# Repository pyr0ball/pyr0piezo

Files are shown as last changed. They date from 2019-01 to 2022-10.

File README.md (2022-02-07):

For more extensive documentation, refer to the [Docs Site](https://docs.pyroballpcbs.com) (source included in this repository)

Presenting...

---

# The Pyr0-Piezo Z-Axis Sensor

## What is this thing?

TL;DR: It's a litte circuit that turns your actual nozzle into a z-probe.

This is a Z-Probe Sensor for 3D Printers that utilizes a piezoelectric element (commonly a 20-27mm piezo disk used in musical pickups) to detect when the nozzle of the printer touches the bed. There have been other Z-Probes in the past that do this, but this is the first to incorporate an onboard microcontroller that automatically calibrates and balances the circuit. Previous piezo Z-Probes all required manual tuning to some extent, usually with tiny hard-to-use trimpots. Due to the mechanical and electrical characteristics of this type of sensor, it has several advantages over other Z-Probes:

- There are no offsets to configure or adjust
- It can be configured to emulate either a standard endstop, or any active-high Z-Probe
- It's not dependent on a specific type of bed or hotend
- The builtin signal filtering reduces the amount of false driggers dramatically compared to other piezo sensors.
- It's FAST. Delay between the piezo being actuated and the z-trigger signal being sent to the printer's controller is ***just 26 nanoseconds***

### Is there a catch?

Well, yeah a couple. The sensor requires introducing a small amount of physical instability into the construction of the 3D printer. Something needs to move, even a small fraction of a millimeter. This can be something like the bed being pushed down slightly on it's springs, or adding a hinge and a tensioning spring to the print head. There's innumerable ways to make this work, and I've been working hard with my beta testers to find the best possible method combining as much stability as possble with the highest sensitivity. The other catch is that any oozing filament will skew the leveling results, so you have to decide to either assume there will always be ooze and use a small z-offset, or add a nozzle wipe/clean manuver to your startup gcode before bed leveling.

### How do I use it?

I designed the sensor to connect to a 3D Printer's controller like any other endstop or Z-Probe. The sensor also includes an i2c interface that will allow the 3D Printer's controller to change parameters on the fly depending on the use-case.

The piezo element is mounted somewhere on the 3D Printer in such a way that it undergoes mechanical stress when the nozzle touches the bed. So far there have been three distinct mounting schemes that appear to work well:

- On the extruder assembly
- Under the Print Bed
- In the case of CoreXY or other Gantry Kinematic systems, on either end of the gantry

#### Features:

- Self-calibrating (no more fiddling with tiny potentiometers!)
- Ultra-precise z-height measurements
- Zero offset (The nozzle itself is the sensor!)
- Compatible with ALL surface types
- No plugging in removable sensors for leveling
- Tunable over UART / I2C

#### FFC Cable Chain Extra Features:

- FFC Cable chain for a clean connection between print head and controller
- Onboard switchable DC buck converter for 12v or 5v fan operation
- LED Feedback on all PWM components
 Standalone version available for drop-in installation

Credit must be given to precisionpiezo.co.uk for getting me started on this project and giving me a place to start. I did build a version of the FFC cable chain based on their electrical designs but found the calibration of the circuit to be very fiddly, as the range of value on the potentiometers that was acceptable was very narrow.

I've since started from scratch using my own BOM and designs, while including an onboard microcontroller to handle auto-calibration. Given that every 3D printer is different, I wanted this sensor to be as easy and stable as other sensors available on the market, but with the increased performance of a piezo sensor.

Join our discord for support and to join in realtime discussion for the project:

Discord Banner 1

---

## Contribution:

Please submit all Pull Requests through the **develop** branch!

The support site for this project uses a script to automatically parse git commits for changelog data. There are three categories of commits that should show up in the case log:

- Bugfix `#bugfix`: commits related to fixing something that's broken
- Added Features `#featureadd`: Commits related to adding new functions and features
- Documentation `#docs`: Any commits that deal specifically with the [documentation site](https://docs.pyroballpcbs.com) or comments/instructions contained within the source itself but do not contribute any functional changes

Simply by adding the corresponding tag to the end of the first line of your commit message, the changelog will automatically compile these for the documentation site. Please be sure to include this in any commit messages for this project.

I would also request that commits remain small, adding each change/fix/feature to their own commits. This will help with future debugging, version tracking, and testing.

---

This is a complete redesign from the ground up, but was inspired by the sensor developed by [PrecisionPiezoUK](https://precisionpiezo.co.uk/resources-osh)

Original FFC Cable Chain designs can be found on my Thingiverse:

- [3D Printed Mount for Prusa/Anet printers](https://www.thingiverse.com/thing:2712439)
- [FFC Cable Chain + Piezo boards](https://www.thingiverse.com/thing:2618717)

 Please refer to LICENSE.md for license information

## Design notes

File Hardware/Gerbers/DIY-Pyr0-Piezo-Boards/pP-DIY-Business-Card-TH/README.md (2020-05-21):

# Pyr0-Piezo DIY BusinessCard

This variant of the Pyr0-Piezo circuit utilizes an all Through-Hole design, allowing users to easily solder in their own components.

This circuit also features a full breakout of all of the pins required to connect an external Arduino if the user doesn't want to use an integrated one.

Programming can be performed initially over the onboard ICSP header, and after a bootloader is installed, the user may reprogram the Atmega over the UART header. Alternatively, if the user owns an Arduino Uno with a DIL socket, the Atmega can be programmed using that board and transferred to this one afterward.

Pin assignments are shown on the silkscreen for each header

TODO: Add pin assignments and images

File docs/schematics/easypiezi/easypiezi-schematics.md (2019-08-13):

### EasyPiezi v1.0.0 Schematic

<object data="../Pyr0-Piezo_Standalone_1.0.0_Schematic.pdf" type="application/pdf" width="100%" height="450px">
    <embed src="../Pyr0-Piezo_Standalone_1.0.0_Schematic.pdf">
        <p>This browser does not support PDFs. Please download the PDF to view it: <a href="../Pyr0-Piezo_Standalone_1.0.0_Schematic.pdf">Download PDF</a>.</p>
    </embed>
</object>

### EasyPiezi v1.0.2 Schematic

<object data="../Pyr0-Piezo_Standalone_1.0.2_Schematic.pdf" type="application/pdf" width="100%" height="450px">
    <embed src="../Pyr0-Piezo_Standalone_1.0.2_Schematic.pdf">
        <p>This browser does not support PDFs. Please download the PDF to view it: <a href="../Pyr0-Piezo_Standalone_1.0.2_Schematic.pdf">Download PDF</a>.</p>
    </embed>
</object>

### EasyPiezi v1.1.1 Schematic

<object data="../Pyr0-Piezo_Standalone_PT100_1.1.1_Schematic.pdf" type="application/pdf" width="100%" height="450px">
    <embed src="../Pyr0-Piezo_Standalone_PT100_1.1.1_Schematic.pdf">
        <p>This browser does not support PDFs. Please download the PDF to view it: <a href="../Pyr0-Piezo_Standalone_PT100_1.1.1_Schematic.pdf">Download PDF</a>.</p>
    </embed>
</object>

### EasyPiezi v2.0.0 Schematic

<object data="../Pyr0-Piezo_Standalone_PT100_2.0.0_Schematic.pdf" type="application/pdf" width="100%" height="450px">
    <embed src="../Pyr0-Piezo_Standalone_PT100_2.0.0_Schematic.pdf">
        <p>This browser does not support PDFs. Please download the PDF to view it: <a href="../Pyr0-Piezo_Standalone_PT100_2.0.0_Schematic.pdf">Download PDF</a>.</p>
    </embed>
</object>

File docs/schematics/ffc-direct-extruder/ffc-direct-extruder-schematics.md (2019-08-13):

### FFC Direct Extruder v1.0.2 Schematic

<object data="../Pyr0-Piezo_FFC_Extruder_Board1.0.2_Schematic.pdf" type="application/pdf" width="100%" height="450px">
    <embed src="../Pyr0-Piezo_FFC_Extruder_Board1.0.2_Schematic.pdf">
        <p>This browser does not support PDFs. Please download the PDF to view it: <a href="../Pyr0-Piezo_FFC_Extruder_Board1.0.2_Schematic.pdf">Download PDF</a>.</p>
    </embed>
</object>

### FFC Direct Extruder v1.1.0 Schematic

<object data="../Pyr0-Piezo_FFC_Extruder_Board1.1.0_Schematic.pdf" type="application/pdf" width="100%" height="450px">
    <embed src="../Pyr0-Piezo_FFC_Extruder_Board1.1.0_Schematic.pdf">
        <p>This browser does not support PDFs. Please download the PDF to view it: <a href="../Pyr0-Piezo_FFC_Extruder_Board1.1.0_Schematic.pdf">Download PDF</a>.</p>
    </embed>
</object>

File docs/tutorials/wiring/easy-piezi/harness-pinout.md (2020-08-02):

# EasyPiezi Wiring Harness Pinout

## Main Connector Controller Side

The Main Connector for the EasyPiezi has 6 pins, with Pin1 marked with a small embossed arrow:

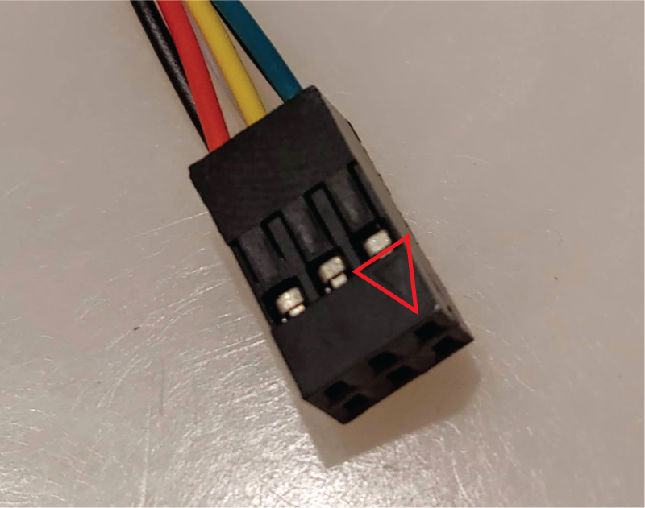
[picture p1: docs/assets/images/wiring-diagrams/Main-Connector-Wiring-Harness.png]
Main Connecctor Wiring Harness Input


Pin numbers are laid out in the following image and table:

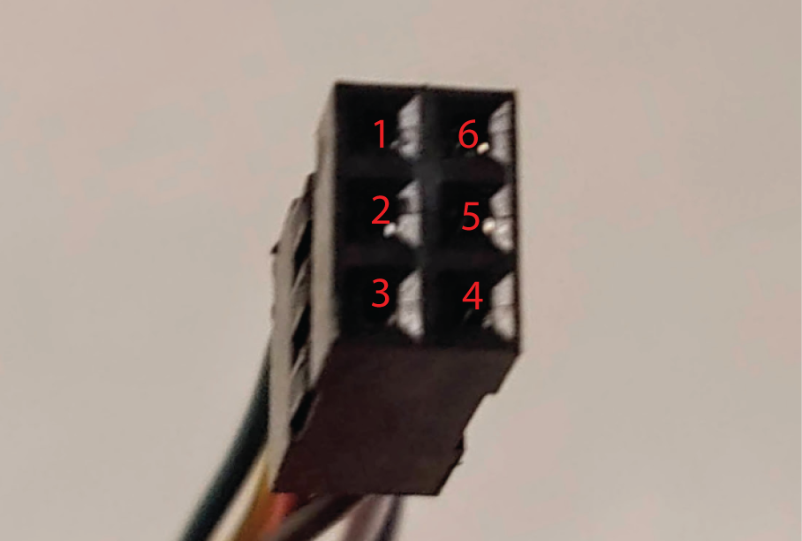
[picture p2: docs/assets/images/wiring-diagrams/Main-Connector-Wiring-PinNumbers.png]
Input Connector Pin Assignments


| Pin Number | Wire Color | Signal Name | Req/Opt |
|---|---|---|---|
| 1 | <strong><span style="color:green">Green</span></strong> | SDA (I2C) | Optional|
| 2 | <strong><span style="color:yellow; background-color:#212121; ">Yellow</span></strong> | SCL (I2C) | Optional|
| 3 | <strong><span style="color:red">Red</span></strong> | +6-12V DC | Required|
| 4 | <strong><span style="color:black; background-color:#F5F5F5;">Black</span></strong> | Ground | Required|
| 5 | <strong><span style="color:white; background-color:#212121">White</strong> | Z-Trigger | Required|
| 6 | <strong><span style="color:#08F">Blue</strong> | PT100 Anlg  | Optional|

## Main Connector Sensor Side

The EasyPiezi's Main Connector Pinout is printed on the bottom of the board:

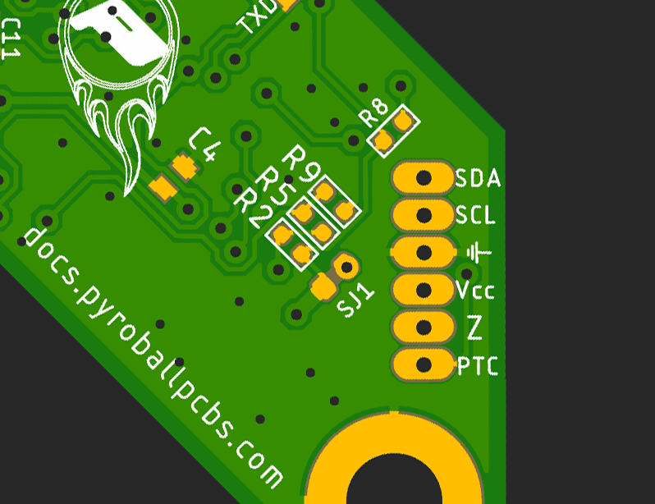
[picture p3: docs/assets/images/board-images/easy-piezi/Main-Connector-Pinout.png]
EasyPiezi Board Main Connector Pinout


They are arranged from top to bottom:

| Pin Number | Wire Color | Signal Name | Req/Opt |
|---|---|---|---|
| 1 | <strong><span style="color:green">Green</span></strong> | SDA (I2C) | Optional|
| 2 | <strong><span style="color:yellow; background-color:#212121; ">Yellow</span></strong> | SCL (I2C) | Optional|
| 3 | <strong><span style="color:black; background-color:#aaa;">Black</span></strong> | Ground | Required|
| 4 | <strong><span style="color:red">Red</span></strong> | +6-12V DC | Required|
| 5 | <strong><span style="color:white; background-color:#212121">White</strong> | Z-Trigger | Required|
| 6 | <strong><span style="color:#08F">Blue</strong> | PT100 Anlg  | Optional|

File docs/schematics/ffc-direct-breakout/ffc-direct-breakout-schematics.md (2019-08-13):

### FFC Direct Breakout v1.0.0 Schematic

<object data="../Pyr0-Piezo_FFC_Breakout_1.0.0_Schematic.pdf" type="application/pdf" width="100%" height="450px">
    <embed src="../Pyr0-Piezo_FFC_Breakout_1.0.0_Schematic.pdf">
        <p>This browser does not support PDFs. Please download the PDF to view it: <a href="../Pyr0-Piezo_FFC_Breakout_1.0.0_Schematic.pdf">Download PDF</a>.</p>
    </embed>
</object>

### FFC Direct Breakout v2.0.0 Schematic

<object data="../Pyr0-Piezo_FFC_Breakout_2.0.0_Schematic.pdf" type="application/pdf" width="100%" height="450px">
    <embed src="../Pyr0-Piezo_FFC_Breakout_2.0.0_Schematic.pdf">
        <p>This browser does not support PDFs. Please download the PDF to view it: <a href="../Pyr0-Piezo_FFC_Breakout_2.0.0_Schematic.pdf">Download PDF</a>.</p>
    </embed>
</object>

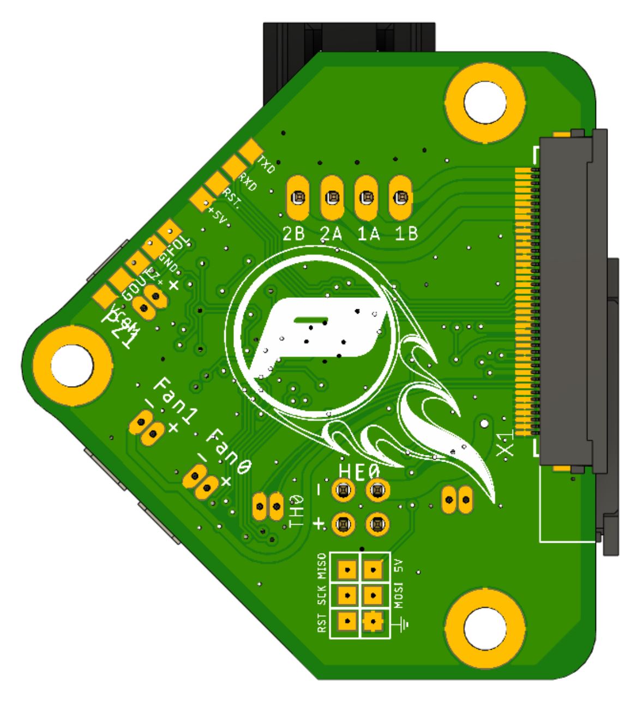
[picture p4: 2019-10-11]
docs/assets/images/board-images/pp-ffc/Pyr0-Piezo-FFC-Direct-Extruder_v2.1.2_Bot.JPG

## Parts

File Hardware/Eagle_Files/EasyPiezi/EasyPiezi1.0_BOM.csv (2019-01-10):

Qty | Value | Device | Package | Parts | Description | AVAILABILITY | DESCRIPTION | MANUFACTURER_PART_NUMBER | MF | MP | MPN | OC_FARNELL | OC_NEWARK | PACKAGE | PRICE | TP_SIGNAL_NAME | VALUE | VENDOR
4 |  | SEEED-LED_SMD-LED-CLEAR-BLUE(0603)LED_0603 | SEEED-LED_LED-0603 | ERR, PWR, TRG, Z_TRG | 304090045
3 |  | SMD-RES-0R-5%-1/16W(0402) | R0402 | R6, R8, R16 | 301010000 |  |  |  |  |  | RC0402JR-070RL |  |  |  |  |  | 0R
1 | 0.1uF | CERAMIC-1NF-50V-10%-X7R(0402)CAP_0402 | CAPC1005X50 | C3 | 302010005
1 | 100R | SMD-RES-0R-5%-1/16W(0402) | R0402 | R15 | 301010000 |  |  |  |  |  | RC0402JR-070RL |  |  |  |  |  | 0R
3 | 10K | SMD-RES-0R-5%-1/16W(0402) | R0402 | R3, R5, R10 | 301010000 |  |  |  |  |  | RC0402JR-070RL |  |  |  |  |  | 0R
2 | 1M | SMD-RES-0R-5%-1/16W(0402) | R0402 | R1, R4 | 301010000 |  |  |  |  |  | RC0402JR-070RL |  |  |  |  |  | 0R
2 | 1uF | SEEED-CAPACITOR_CERAMIC-10UF-25V-10%-X5R(0805)CAP_0603_GEN | CAPC1609X80 | C1, C2 | 302010178
2 | 220R | SMD-RES-0R-5%-1/16W(0402) | R0402 | R9, R11 | 301010000 |  |  |  |  |  | RC0402JR-070RL |  |  |  |  |  | 0R
1 | 3.3K | SMD-RES-0R-5%-1/16W(0402) | R0402 | R2 | 301010000 |  |  |  |  |  | RC0402JR-070RL |  |  |  |  |  | 0R
2 | 330R | SMD-RES-0R-5%-1/16W(0402) | R0402 | R12, R13 | 301010000 |  |  |  |  |  | RC0402JR-070RL |  |  |  |  |  | 0R
1 | 470R | SMD-RES-0R-5%-1/16W(0402) | R0402 | R14 | 301010000 |  |  |  |  |  | RC0402JR-070RL |  |  |  |  |  | 0R
1 | 680R | SMD-RES-0R-5%-1/16W(0402) | R0402 | R7 | 301010000 |  |  |  |  |  | RC0402JR-070RL |  |  |  |  |  | 0R
1 | ATMEGA48PA-MMHR28M1-L | ATMEGA48PA-MMHR28M1-L | 28M1-L | U1 |  |  |  | ATMEGA48PAMMHR |  |  |  |  |  |  |  |  |  | Atmel
1 | BAV199 | BAV199 | SOT23 | D8 | DIODE
1 | CON-MOLEX-2P-1.27MM048 | CON-MOLEX-2P-1.27MM048 | 53048-02 | PZ1 | CONNECTOR |  |  |  | MOLEX |  | 53048-0210 | 1012259 | 57H4718
1 | CON-MOLEX-3P-1.25MM048 | CON-MOLEX-3P-1.25MM048 | 53048-03 | J1 | CONNECTOR |  |  |  | WALDOM/MOLEX |  | 53048-0310 | 9732918 | 38C9908
2 | HOLES_MOUNT-PAD-ROUND2.8 | HOLES_MOUNT-PAD-ROUND2.8 | HOLES_2,8-PAD | H2, H3 | MOUNTING PAD, round
1 | L78L05ACU | L78L05ACU | SOT89 | U2 | 5V Positive voltage regulator SMD SOT89 Package | Unavailable | Voltage regulator | fixed | 5V | 0.1A | SOT89 | SMD | Package: reel, tape |  | STMicroelectronics | L78L05ACU-TR
1 | LM358PWRDFN-8 | LM358PWRDFN-8 | SON50P200X200X60-9N | U3
1 | MCP6001T-I/OTSOT-23-5_MC-L | MCP6001T-I/OTSOT-23-5_MC-L | SOT-23-5_MC-L | U4 |  |  |  | MCP6001TIOT |  |  |  |  |  |  |  |  |  | Microchip
2 | TPTP06R | TPTP06R | TP06R | INT, SS | Test pad
13 | TPTP13SQ | TPTP13SQ | TP13SQ | +5V, 5V, GND, MISO, MOSI, RST, RST., RXD, SCK, SCL, SDA, TXD, ⏚ | Test pad

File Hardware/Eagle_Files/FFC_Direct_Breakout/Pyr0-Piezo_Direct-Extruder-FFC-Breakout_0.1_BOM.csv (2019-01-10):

Qty | Value | Device | Package | Parts | Description | AVAILABILITY | DESCRIPTION | MANUFACTURER_PART_NUMBER | MF | MP | MPN | OC_FARNELL | OC_NEWARK | PACKAGE | PRICE | VALUE | VENDOR
2 |  | KK-156-2 | KK-156-2 | HE0, PWR | KK 156 HEADER |  |  |  | MOLEX |  |  | unknown | unknown
2 |  | LEDCHIP-LED0805 | CHIP-LED0805 | 5V, 12V | LED
1 |  | SEEED-SWITCH_DIP-TOGGLE-SWITCH-2CH-(2X3P-2.54)DPDT_254_6P_UPDATE | SEEED-SWITCH_SW6-2.54-9.0X3.5X3.2+2.0MM | SW1 | 311010004
1 | 100R | SMD-RES-2K-5%-1/8W(0805) | R0805 | R5 | 301010318 |  |  |  |  |  | RC0805JR-072KL |  |  |  |  | 2K
1 | 10R | SMD-RES-2K-5%-1/8W(0805) | R0805 | R7 | 301010318 |  |  |  |  |  | RC0805JR-072KL |  |  |  |  | 2K
1 | 10uF | SEEED-CAPACITOR_CERAMIC-10UF-25V-10%-X5R(0805)CAP_0805-3D | CAPC2012X130 | C5 | 302010178
1 | 1K | SEEED-RESISTOR_SMD-RES-1.5K-1%-1/10W(0603)DETAILED_MODEL | SEEED-RESISTOR_R0603 | R4 | 301010189
1 | 1R | SMD-RES-2K-5%-1/8W(0805) | R0805 | R6 | 301010318 |  |  |  |  |  | RC0805JR-072KL |  |  |  |  | 2K
1 | 2.05K | SEEED-RESISTOR_SMD-RES-1.5K-1%-1/10W(0603)DETAILED_MODEL | SEEED-RESISTOR_R0603 | R3 | 301010189
4 | 220uf | DIP-ALUMINUM-100UF-16V(D5-H7MM) | PC-D5.3MM | C1, C2, C3, C4 | 302030031 |  |  |  |  |  | KS 100uF/16V |  |  |  |  | 100uf
1 | 240R | SEEED-RESISTOR_SMD-RES-1.5K-1%-1/10W(0603)DETAILED_MODEL | SEEED-RESISTOR_R0603 | R1 | 301010189
1 | 2N2222TO92 | 2N2222TO92 | TO92 | Q1 | NPN TRANSISTOR
1 | 2N2907 | 2N2907 | TO92 | Q2 | NPN TRANSISTOR
1 | 715R | SEEED-RESISTOR_SMD-RES-1.5K-1%-1/10W(0603)DETAILED_MODEL | SEEED-RESISTOR_R0603 | R2 | 301010189
4 | C-GRID-02-70553 | C-GRID-02-70553 | 70553-02 | FAN0, FAN1, TH0, Z_MIN | CONNECTOR |  |  |  | MOLEX |  |  | unknown | unknown
1 | C-GRID-04-70553 | C-GRID-04-70553 | 70553-04 | E0 | CONNECTOR |  |  |  | MOLEX |  |  | unknown | unknown
4 | HOLES_MOUNT-PAD-ROUND3.2 | HOLES_MOUNT-PAD-ROUND3.2 | HOLES_3,2-PAD | H1, H2, H3, H4 | MOUNTING PAD, round
1 | L78L05ACU | L78L05ACU | SOT89 | U2 | 5V Positive voltage regulator SMD SOT89 Package | Unavailable | Voltage regulator | fixed | 5V | 0.1A | SOT89 | SMD | Package: reel, tape |  | STMicroelectronics | L78L05ACU-TR
1 | LM317DCY | LM317DCY | SOT230P700X180-4N | U1 | IC ADJ LINEAR REG 1.25V TO 37V | Unavailable | IC Regulator LM317/SOT223/LM317DCY TEXAS INSTRUMENT RoHS Ampere=1.5 SOT223 |  | Texas Instruments | LM317DCY |  |  |  | SOT-223-4 Texas Instruments | None
1 | SFW24R-1STE1LF | SFW24R-1STE1LF | CON24_1X24_DRB_SFW | J1 |  |  |  | SFW24R1STE1LF |  |  |  |  |  |  |  |  | FCI

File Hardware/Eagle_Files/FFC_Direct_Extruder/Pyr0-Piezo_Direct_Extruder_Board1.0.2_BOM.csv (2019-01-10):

Qty | Value | Device | Package | Parts | Description | MANUFACTURER_PART_NUMBER | MF | MPN | OC_FARNELL | OC_NEWARK | TP_SIGNAL_NAME | VALUE | VENDOR
7 |  | SEEED-LED_SMD-LED-CLEAR-BLUE(0603)LED_0603 | SEEED-LED_LED-0603 | D2, D3, D4, D5, ERR, PWR, TRG | 304090045
1 |  | SMD-RES-0R-5%-1/16W(0402) | R0402 | R6 | 301010000 |  |  | RC0402JR-070RL |  |  |  | 0R
2 | 0.1uF | CERAMIC-1NF-50V-10%-X7R(0402)CAP_0402 | CAPC1005X50 | C1, C2 | 302010005
1 | 0R | SEEED-RESISTOR_SMD-RES-1.5K-1%-1/10W(0603)DETAILED_MODEL | SEEED-RESISTOR_R0603 | R14 | 301010189
1 | 100R | SMD-RES-0R-5%-1/16W(0402) | R0402 | R13 | 301010000 |  |  | RC0402JR-070RL |  |  |  | 0R
3 | 10K | SMD-RES-0R-5%-1/16W(0402) | R0402 | R2, R4, R10 | 301010000 |  |  | RC0402JR-070RL |  |  |  | 0R
2 | 1K | SMD-RES-0R-5%-1/16W(0402) | R0402 | R3, R8 | 301010000 |  |  | RC0402JR-070RL |  |  |  | 0R
2 | 1M | SMD-RES-0R-5%-1/16W(0402) | R0402 | R1, R19 | 301010000 |  |  | RC0402JR-070RL |  |  |  | 0R
1 | 1N4148DFN-1006-2 | 1N4148DFN-1006-2 | DIOC1006X70 | D1 | DIODE
1 | 1uF | SEEED-CAPACITOR_CERAMIC-10UF-25V-10%-X5R(0805)CAP_0603_GEN | CAPC1609X80 | C3 | 302010178
2 | 220R | SMD-RES-0R-5%-1/16W(0402) | R0402 | R7, R11 | 301010000 |  |  | RC0402JR-070RL |  |  |  | 0R
1 | 3.3K | SMD-RES-0R-5%-1/16W(0402) | R0402 | R17 | 301010000 |  |  | RC0402JR-070RL |  |  |  | 0R
2 | 330R | SMD-RES-0R-5%-1/16W(0402) | R0402 | R5, R12 | 301010000 |  |  | RC0402JR-070RL |  |  |  | 0R
1 | 470R | SMD-RES-0R-5%-1/16W(0402) | R0402 | R9 | 301010000 |  |  | RC0402JR-070RL |  |  |  | 0R
1 | 680R | SMD-RES-0R-5%-1/16W(0402) | R0402 | R15 | 301010000 |  |  | RC0402JR-070RL |  |  |  | 0R
1 | ATMEGA48PA-MMHR28M1-L | ATMEGA48PA-MMHR28M1-L | 28M1-L | U1 |  | ATMEGA48PAMMHR |  |  |  |  |  |  | Atmel
1 | BAV199 | BAV199 | SOT23 | D8 | DIODE
1 | C-GRID-04-70553 | C-GRID-04-70553 | 70553-04 | E0 | CONNECTOR |  | MOLEX |  | unknown | unknown
4 | CON-MOLEX-2P-1.27MM048 | CON-MOLEX-2P-1.27MM048 | 53048-02 | FAN0, FAN1, PZ1, TH0 | CONNECTOR |  | MOLEX | 53048-0210 | 1012259 | 57H4718
3 | HOLES_MOUNT-PAD-ROUND2.8 | HOLES_MOUNT-PAD-ROUND2.8 | HOLES_2,8-PAD | H1, H2, H3 | MOUNTING PAD, round
1 | JST-2.54-2X2JST-DUPONT-2.54-2X2 | JST-2.54-2X2JST-DUPONT-2.54-2X2 | HDRRAR4W64P254_2X2_556X736X556B | HE0
1 | LM358PWRDFN-8 | LM358PWRDFN-8 | SON50P200X200X60-9N | U3
1 | MCP6001T-I/OTSOT-23-5_MC-L | MCP6001T-I/OTSOT-23-5_MC-L | SOT-23-5_MC-L | U2 |  | MCP6001TIOT |  |  |  |  |  |  | Microchip
1 | SFW24R-1STE1LF | SFW24R-1STE1LF | CON24_1X24_DRB_SFW | J1 |  | SFW24R1STE1LF |  |  |  |  |  |  | FCI
2 | TPTP06R | TPTP06R | TP06R | INT, SS | Test pad
3 | TPTP10R | TPTP10R | TP10R | ADJ+, ADJ-, A_OUT | Test pad
13 | TPTP13SQ | TPTP13SQ | TP13SQ | +5V, 5V, GND, MISO, MOSI, RST, RST., RXD, SCK, SCL, SDA, TXD, ⏚ | Test pad

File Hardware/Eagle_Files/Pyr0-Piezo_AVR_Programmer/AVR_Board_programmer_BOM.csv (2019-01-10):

Qty | Value | Device | Package | Parts | Description | DESCRIPTION | DIGI-KEY_PART_NUMBER | DIGI-KEY_PURCHASE_URL | MF | MP | MPN | PACKAGE | VALUE
3 |  | SEEED-LED_SMD-LED-CLEAR-BLUE(0603)LED_0603 | SEEED-LED_LED-0603 | PWR, RX, TX | 304090045
1 |  | SEEED-SWITCH_SMD-BUTTON(2P-3.0X2.5X1.2+0.4MM)SW2-2.6-3X2.5X1.2 | SEEED-SWITCH_SW2-2.6-3.0X2.5X1.2+0.4MM | RESET | 311020047
2 |  | SMD-RES-0R-5%-1/16W(0402) | R0402 | R3, R8 | 301010000 |  |  |  |  |  | RC0402JR-070RL |  | 0R
1 | 10118192-0001LF | 10118192-0001LF | AMPHENOL_10118192-0001LF | J1 | Single Port 5 Contact Horizontal Right Angle Shielded Micro B USB 2.0 Connector | Conn Micro USB Type B RCP 5 POS 0.65mm Solder RA SMD 5 Terminal 1 Port T/R | 609-4613-1-ND | https://www.digikey.com/product-detail/en/amphenol-fci/10118192-0001LF/609-4613-1-ND/2785378 | Amphenol FCI | 10118192-0001LF |  | None
1 | 22K | SMD-RES-0R-5%-1/16W(0402) | R0402 | R1 | 301010000 |  |  |  |  |  | RC0402JR-070RL |  | 0R
1 | 47K | SMD-RES-0R-5%-1/16W(0402) | R0402 | R2 | 301010000 |  |  |  |  |  | RC0402JR-070RL |  | 0R
1 | CP2102N-A01-GQFN20 | CP2102N-A01-GQFN20 | SILABS_QFN20 | U1 | Ic Bridge Usb To Uart 20qfn | Usb-Uart Interface Bridge, Qfn-20 | 336-3692-ND | https://www.digikey.com/product-detail/en/silicon-labs/CP2102N-A01-GQFN20/336-3692-ND/6012517 | Silicon Labs | CP2102N-A01-GQFN20 |  | QFN-20 Silicon Labs
3 | HOLES_MOUNT-PAD-ROUND2.8 | HOLES_MOUNT-PAD-ROUND2.8 | HOLES_2,8-PAD | H1, H2, H3 | MOUNTING PAD, round
1 | JST-2.54MM_5P-2.54JST_2.54MM_5P_F | JST-2.54MM_5P-2.54JST_2.54MM_5P_F | HDRVR5W64P254_1X5_1270X254X575B | TTL
1 | SP0503BAHTG | SP0503BAHTG | SOT143 | D1 | TVS DIODE 5.5VWM 8.5VC SOT143 | SP050xBA Series 8 V 30 pF Uni-Directional SMT TVS Avalanche Diode Array SOT-143 | F2715CT-ND | https://www.digikey.com/product-detail/en/littelfuse-inc/SP0503BAHTG/F2715CT-ND/1154322 | Littelfuse Inc. | SP0503BAHTG |  | SOT-143 Littelfuse
5 | TP | TP | TP13SQ-HOLE | +5V, GND, RST., RXD, TXD | Test pad

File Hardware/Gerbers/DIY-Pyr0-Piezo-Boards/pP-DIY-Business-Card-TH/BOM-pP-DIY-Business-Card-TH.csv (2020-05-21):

Qty | Value | Package | References | Description | MF | MPN | OC_DIGIKEY | OC_FARNELL | OC_NEWARK | SPICEPREFIX
7 | 0.1uF | TH | C1, C2, C3, C4, C17, C18, C19 | CAPACITOR, European symbol |  |  | 2368-CML104M50-ND |  |  | C
3 | 100R | TH | R10, R12, R17 | RESISTOR, European symbol |  |  | RMCF0805JT100RCT-ND |  |  | R
6 | 10K | TH | R5, R6, R9, R15, R16, R18 | RESISTOR, European symbol |  |  | CR0805-JW-103ELFCT-ND |  |  | R
1 | 10nF | TH | C20 | CAPACITOR, European symbol |  |  | 2368-CML103M50-ND |  |  | C
2 | 10uF | TH | C21, C23 | CAPACITOR, European symbol |  |  | 478-7366-1-ND |  |  | C
5 | 1K | TH | R1, R3, R4, R7, R11 | RESISTOR, European symbol |  |  | RMCF0805JT1K00CT-ND |  |  | R
2 | 1M | TH | R2, R8 | RESISTOR, European symbol |  |  | CR0805-JW-105ELFCT-ND |  |  | R
2 | 1N4004 | TH | D1, D2 | DIODE |  |  |  |  |  | D
3 | 1uF | TH | C16, C22, C24 | CAPACITOR, European symbol |  |  | 2368-CML105M50-ND |  |  | C
2 | 2K2 | TH | R13, R14 | RESISTOR, European symbol |  |  | RMCF0805JT2K20CT-ND |  |  | R
1 | 3K3 | TH | R20 | RESISTOR, European symbol |  |  | RMCF0805JT3K30CT-ND |  |  | R
1 | 4K7 | TH | R19 | RESISTOR, European symbol |  |  | RMCF0805JT4K70CT-ND |  |  | R
1 | ATMEGA328P | DIP28 | U2 |  |  |  | ATMEGA328-PU-ND |  |  | U
2 | C-GRID-02-70553 | 70553-02 | PT100, PZ-IN | CONNECTOR | MOLEX |  |  | unknown | unknown
1 | JST-2.54MM_3PX2JST-2.54MM_3PX2 | Dupont_2x3_STR | ICSP | 2.54mm Dupont Female header 3x2p 6-positions
1 | JST-2.54MM_5P-2.54JST_2.54MM_5P_F | Dupont_1x5_RA | UART | 2.54mm Dupont Female Header 1x5p 5-positions
1 | LM2902N | DIL14 | U1 | Low power quad operational amplifier
1 | PP-STANDALONE-HEADER | Dupont_2x6_RA | J1 | 2.54mm Dupont Male Header Right 2x6 12-positions
1 | LED-3mm Green | SFH482 | PWR | 3mm LED
1 | LED-3mm Blue | SFH482 | TRIG | 3mm LED

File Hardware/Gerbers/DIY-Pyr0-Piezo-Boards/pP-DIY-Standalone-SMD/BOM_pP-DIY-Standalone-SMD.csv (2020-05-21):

Qty | References | Value | Package | Description | MF | MPN | OC_FARNELL | OC_NEWARK
1 | PWR | GREEN | LED0805 | LED SMD 0805
1 | TRIG | BLUE | LED0805 | LED SMD 0805
6 | C1, C2, C4, C17, C18, C19 | 0.1uF | C0805
3 | R10, R12, R17 | 100R | R0805
5 | R5, R6, R9, R15, R16 | 10K | R0805
1 | C20 | 10nF | C0805
2 | C21, C23 | 10uF | C0805
5 | R1, R3, R4, R7, R11 | 1K | R0805
2 | R2, R8 | 1M | R0805
1 | C16 | 1uF | C0805
2 | R13, R14 | 2K2 | R0805
2 | C22, C24 | 3.3uF | C0805
1 | R19 | 4K7 | R0805
1 | D1 | BAV99 | SOT23 | DIODE
2 | PT1, PZ | C-GRID-02-70553 | 70553-02 | CONNECTOR | MOLEX
1 | U1 | LM2902D | SO14 | Low power quad operational amplifier
1 | J1 | PP-STANDALONE-HEADER | Dupont 2.54mm 2x6 RA

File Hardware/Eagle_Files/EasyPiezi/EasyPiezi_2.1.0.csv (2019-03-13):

Part | Value | Device | Package | Description | AVAILABILITY | DESCRIPTION | MF | MP | MPN | OC_FARNELL | OC_NEWARK | PACKAGE | PRICE | PROD_ID | TP_SIGNAL_NAME | VALUE
+5V | TPTP13SQ | TPTP13SQ | TP13SQ | Test pad
5V | TPTP13SQ | TPTP13SQ | TP13SQ | Test pad
ADJ+ | TPTP13SQ | TPTP13SQ | TP13SQ | Test pad
ADJ- | TPTP13SQ | TPTP13SQ | TP13SQ | Test pad
C1 | 1uF | SEEED-CAPACITOR_CERAMIC-10UF-25V-10%-X5R(0805)CAP_0603_GEN | CAPC1609X80 | 302010178
C2 | 1uF | SEEED-CAPACITOR_CERAMIC-10UF-25V-10%-X5R(0805)CAP_0603_GEN | CAPC1609X80 | 302010178
C3 | 0.1uF | CERAMIC-1NF-50V-10%-X7R(0402)CAP_0402 | CAPC1005X50 | 302010005
C4 | 0.1uF | CERAMIC-1NF-50V-10%-X7R(0402)CAP_0402 | CAPC1005X50 | 302010005
C5 | 0.1uF | CERAMIC-1NF-50V-10%-X7R(0402)CAP_0402 | CAPC1005X50 | 302010005
C6 | 0.1uF | CERAMIC-1NF-50V-10%-X7R(0402)CAP_0402 | CAPC1005X50 | 302010005
C7 | 1uF | CERAMIC-1NF-50V-10%-X7R(0402)CAP_0402 | CAPC1005X50 | 302010005
C8 | 0.1uF | CERAMIC-1NF-50V-10%-X7R(0402)CAP_0402 | CAPC1005X50 | 302010005
C9 | 0.1uF | CERAMIC-1NF-50V-10%-X7R(0402)CAP_0402 | CAPC1005X50 | 302010005
C10 | 0.1uF | CERAMIC-1NF-50V-10%-X7R(0402)CAP_0402 | CAPC1005X50 | 302010005
C11 | 10nF | CERAMIC-1NF-50V-10%-X7R(0402)CAP_0402 | CAPC1005X50 | 302010005
C12 | 10uF | CERAMIC-1NF-50V-10%-X7R(0402)CAP_0402 | CAPC1005X50 | 302010005
C13 | 3.3uF | CERAMIC-1NF-50V-10%-X7R(0402)CAP_0402 | CAPC1005X50 | 302010005
C14 | 10uF | CERAMIC-1NF-50V-10%-X7R(0402)CAP_0402 | CAPC1005X50 | 302010005
C15 | 3.3uF | CERAMIC-1NF-50V-10%-X7R(0402)CAP_0402 | CAPC1005X50 | 302010005
D1 | ZENER_DIODE_PLZ5V1C | ZENER_DIODE_PLZ5V1C | DO-219AC
D8 | BAV199 | BAV199 | SOT23 | DIODE
F1 | 500mA | SMD-RES-0R-5%-1/16W(0402) | R0402 | 301010000 |  |  |  |  | RC0402JR-070RL |  |  |  |  |  |  | 0R
GND | TPTP13SQ | TPTP13SQ | TP13SQ | Test pad
H2 | HOLES_MOUNT-PAD-ROUND2.8 | HOLES_MOUNT-PAD-ROUND2.8 | HOLES_2,8-PAD | MOUNTING PAD, round
H3 | HOLES_MOUNT-PAD-ROUND2.8 | HOLES_MOUNT-PAD-ROUND2.8 | HOLES_2,8-PAD | MOUNTING PAD, round
INT | TPTP06R | TPTP06R | TP06R | Test pad
J1 | CON-MOLEX-6P-1.25MM048 | CON-MOLEX-6P-1.25MM048 | 53048-06 | CONNECTOR |  |  | WALDOM/MOLEX |  | 53048-0610 | 1012260 | 38C9911
J2 |  | SEEED-RESISTOR_SMD-RES-1.5K-1%-1/10W(0603)DETAILED_MODEL | SEEED-RESISTOR_R0603 | 301010189
LED | LED-RGB-COM_ANO0606 | LED-RGB-COM_ANO0606 | 0606_LED | Everlight Electronics Co Ltd EAST1616RGBB4 0606 RGB LED |  |  |  |  |  |  |  |  |  | DIO-12140
MISO | TPTP13SQ | TPTP13SQ | TP13SQ | Test pad
MOSI | TPTP13SQ | TPTP13SQ | TP13SQ | Test pad
PT100 | CON-MOLEX-2P-1.27MM048 | CON-MOLEX-2P-1.27MM048 | 53048-02 | CONNECTOR |  |  | MOLEX |  | 53048-0210 | 1012259 | 57H4718
PZ+ | TPTP13SQ | TPTP13SQ | TP13SQ | Test pad
PZ1 | CON-MOLEX-2P-1.27MM048 | CON-MOLEX-2P-1.27MM048 | 53048-02 | CONNECTOR |  |  | MOLEX |  | 53048-0210 | 1012259 | 57H4718
R1 | 1M | SMD-RES-0R-5%-1/16W(0402) | R0402 | 301010000 |  |  |  |  | RC0402JR-070RL |  |  |  |  |  |  | 0R
R3 | 10K | SMD-RES-0R-5%-1/16W(0402) | R0402 | 301010000 |  |  |  |  | RC0402JR-070RL |  |  |  |  |  |  | 0R
R4 | 1M | SMD-RES-0R-5%-1/16W(0402) | R0402 | 301010000 |  |  |  |  | RC0402JR-070RL |  |  |  |  |  |  | 0R
R6 |  | SMD-RES-0R-5%-1/16W(0402) | R0402 | 301010000 |  |  |  |  | RC0402JR-070RL |  |  |  |  |  |  | 0R
R7 | 10K | SMD-RES-0R-5%-1/16W(0402) | R0402 | 301010000 |  |  |  |  | RC0402JR-070RL |  |  |  |  |  |  | 0R
R8 |  | SMD-RES-0R-5%-1/16W(0402) | R0402 | 301010000 |  |  |  |  | RC0402JR-070RL |  |  |  |  |  |  | 0R
R10 | 10K | SMD-RES-0R-5%-1/16W(0402) | R0402 | 301010000 |  |  |  |  | RC0402JR-070RL |  |  |  |  |  |  | 0R
R14 | 1K | SMD-RES-0R-5%-1/16W(0402) | R0402 | 301010000 |  |  |  |  | RC0402JR-070RL |  |  |  |  |  |  | 0R
R15 | 100R | SMD-RES-0R-5%-1/16W(0402) | R0402 | 301010000 |  |  |  |  | RC0402JR-070RL |  |  |  |  |  |  | 0R
R17 | 10K | SMD-RES-0R-5%-1/16W(0402) | R0402 | 301010000 |  |  |  |  | RC0402JR-070RL |  |  |  |  |  |  | 0R
R18 | 10K | SMD-RES-0R-5%-1/16W(0402) | R0402 | 301010000 |  |  |  |  | RC0402JR-070RL |  |  |  |  |  |  | 0R
R19 | 2K2 | SMD-RES-0R-5%-1/16W(0402) | R0402 | 301010000 |  |  |  |  | RC0402JR-070RL |  |  |  |  |  |  | 0R
R20 | 2K2 | SMD-RES-0R-5%-1/16W(0402) | R0402 | 301010000 |  |  |  |  | RC0402JR-070RL |  |  |  |  |  |  | 0R
R21 | 100R | SMD-RES-0R-5%-1/16W(0402) | R0402 | 301010000 |  |  |  |  | RC0402JR-070RL |  |  |  |  |  |  | 0R
R22 | 100R | SMD-RES-0R-5%-1/16W(0402) | R0402 | 301010000 |  |  |  |  | RC0402JR-070RL |  |  |  |  |  |  | 0R
RDY |  | SEEED-LED_SMD-LED-CLEAR-BLUE(0603)LED_0603 | SEEED-LED_LED-0603 | 304090045
RP1 | 1K | RESISTOR_NETWORK_X40804_L | EXBN8V-L
RST | TPTP13SQ | TPTP13SQ | TP13SQ | Test pad
RST. | TPTP13SQ | TPTP13SQ | TP13SQ | Test pad
RXD | TPTP13SQ | TPTP13SQ | TP13SQ | Test pad
SCK | TPTP13SQ | TPTP13SQ | TP13SQ | Test pad
SJ1 |  | SJM | SJM | SMD solder JUMPER
SS | TPTP06R | TPTP06R | TP06R | Test pad
TP1 | TPTP09R | TPTP09R | TP09R | Test pad
TP2 | TPTP09R | TPTP09R | TP09R | Test pad
TXD | TPTP13SQ | TPTP13SQ | TP13SQ | Test pad
U2 | L78L05ACU | L78L05ACU | SOT89 | 5V Positive voltage regulator SMD SOT89 Package | Unavailable | Voltage regulator | fixed | 5V | 0.1A | SOT89 | SMD | Package: reel, tape | STMicroelectronics | L78L05ACU-TR
U3 | LM2902QT | LM2902QT | QFN16 | Low power quad operational amplifier
U4 | ATMEGA48/88/168/328PB | ATMEGA48/88/168/328PB | QFN50P500X500X90-33N | AVR 32KBytes Flash, 1KBytes EEPROM, 2KBytes RAM, w - 20MHZ, QFN/MFL, IND TEMP, GREEN 5 V/ DFN/QFN (M) | Unavailable | AVR 32KBytes Flash, 1KBytes EEPROM, 2KBytes RAM, w - 20MHZ, QFN/MFL, IND TEMP, GREEN 5 V/ DFN/QFN _M_ | Microchip | ATMEGA328PB-MU |  |  |  | VFQFN-32 Microchip | None
⏚ | TPTP13SQ | TPTP13SQ | TP13SQ | Test pad

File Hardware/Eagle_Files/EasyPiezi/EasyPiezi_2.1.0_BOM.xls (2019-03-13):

Designator | MPN | QTY | Link
C1,C2,C7 | CL10A105KO8NNNC | 30 | https://www.digikey.com/product-detail/en/samsung-electro-mechanics/CL10A105KO8NNNC/1276-1034-2-ND/3886692
C3,C4,C5,C6,C8,C9,C10 | CL05F104ZO5NNNC | 70 | https://www.digikey.com/product-detail/en/samsung-electro-mechanics/CL05F104ZO5NNNC/1276-1004-2-ND/3886662
C11 | CL05B103KB5NFNC | 10 | https://www.digikey.com/product-detail/en/samsung-electro-mechanics/CL05B103KB5NFNC/1276-1499-2-ND/3887157
C12,C14 | GRM155C80J106ME11J | 20 | https://www.digikey.com/product-detail/en/murata-electronics-north-america/GRM155C80J106ME11J/490-18210-2-ND/9867918
C13,C15 | GRM155R60J475ME47D | 20 | https://www.digikey.com/product-detail/en/murata-electronics-north-america/GRM155R60J475ME47D/490-5915-2-ND/3694656
D1 | PLZ5V1C | 10 | https://www.digikey.com/product-detail/en/vishay-semiconductor-diodes-division/PLZ5V1C-G3-H/PLZ5V1C-G3-HGITR-ND/7594405
D8 | BAV199-7-F | 10 | https://www.digikey.com/product-detail/en/diodes-incorporated/BAV199-7-F/BAV199-FDITR-ND/1033645
F1 | ERB-RD0R50X | 10 | https://www.digikey.com/product-detail/en/panasonic-electronic-components/ERB-RD0R50X/P15122TR-ND/2796780
LED | IN-S66TATRGB | 10 | https://www.digikey.com/product-detail/en/inolux/IN-S66TATRGB/1830-1077-2-ND/7604943
R1,R4 | RMCF0402JT1M00 | 20 | https://www.digikey.com/product-detail/en/stackpole-electronics-inc/RMCF0402JT1M00/RMCF0402JT1M00TR-ND/1758203
R3,R7,R10,R17,R18 | RMCF0402JT10K0 | 50 | https://www.digikey.com/product-detail/en/stackpole-electronics-inc/RMCF0402JT10K0/RMCF0402JT10K0TR-ND/1758206
R6,R14 | CRG0402J1K0 | 20 | https://www.digikey.com/product-detail/en/te-connectivity-passive-product/CRG0402J1K0/A106129TR-ND/2389662
R8 | RC1005J332CS | 10 | https://www.digikey.com/product-detail/en/samsung-electro-mechanics/RC1005J332CS/1276-4388-2-ND/3964695
R15,R21,R22 | RMCF0402JT100R | 30 | https://www.digikey.com/product-detail/en/stackpole-electronics-inc/RMCF0402JT100R/RMCF0402JT100RTR-ND/1758155
R19,R20 | RMCF0402JT2K20 | 20 | https://www.digikey.com/product-detail/en/stackpole-electronics-inc/RMCF0402JT2K20/RMCF0402JT2K20TR-ND/1712400
RDY | LNJ812K8SRA | 10 | https://www.digikey.com/product-detail/en/panasonic-electronic-components/LNJ812K8SRA/P11472CT-ND/440504
RP1 | EXB-N8V102JX | 10 | https://www.digikey.com/product-detail/en/panasonic-electronic-components/EXB-N8V102JX/Y10102TR-ND/671522
U2 | L78L05A | 10 | https://www.digikey.com/product-detail/en/stmicroelectronics/L78L05ACUTR/497-1183-2-ND/585707
U3 | LM2902Q4T | 10 | https://www.digikey.com/product-detail/en/stmicroelectronics/LM2902Q4T/497-12417-2-ND/2832879
U4 | ATMEGA328PB-MU | 10 | https://www.digikey.com/product-detail/en/microchip-technology/ATMEGA328PB-MU/ATMEGA328PB-MU-ND/5638814

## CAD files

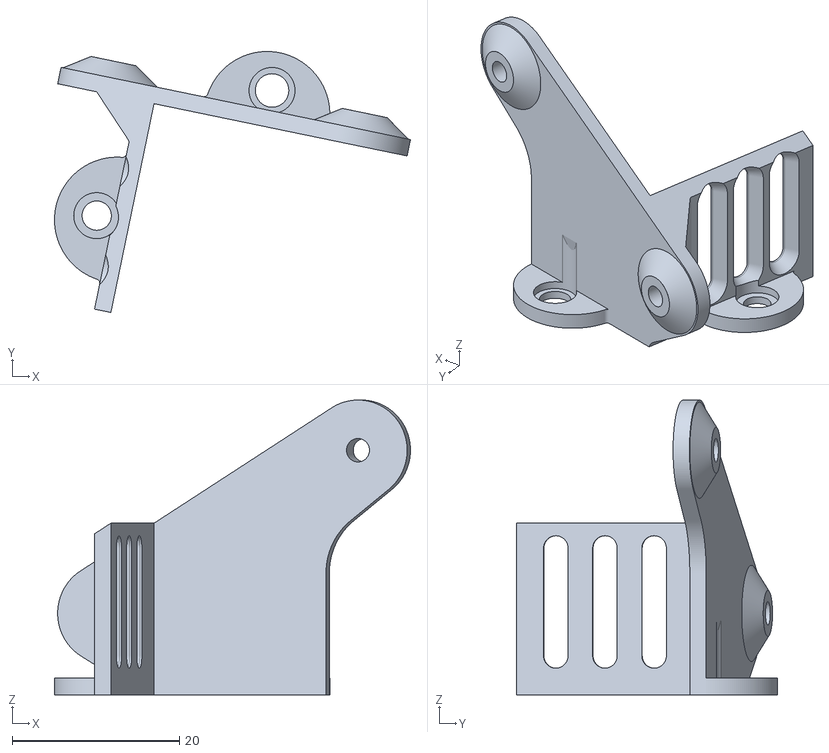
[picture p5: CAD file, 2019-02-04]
3D_Models/3D_Printed_Parts/Printer_Mounts/Creality_Series/Creality-Standalone-Board Mount.stl
42.6 x 31.2 x 35.3

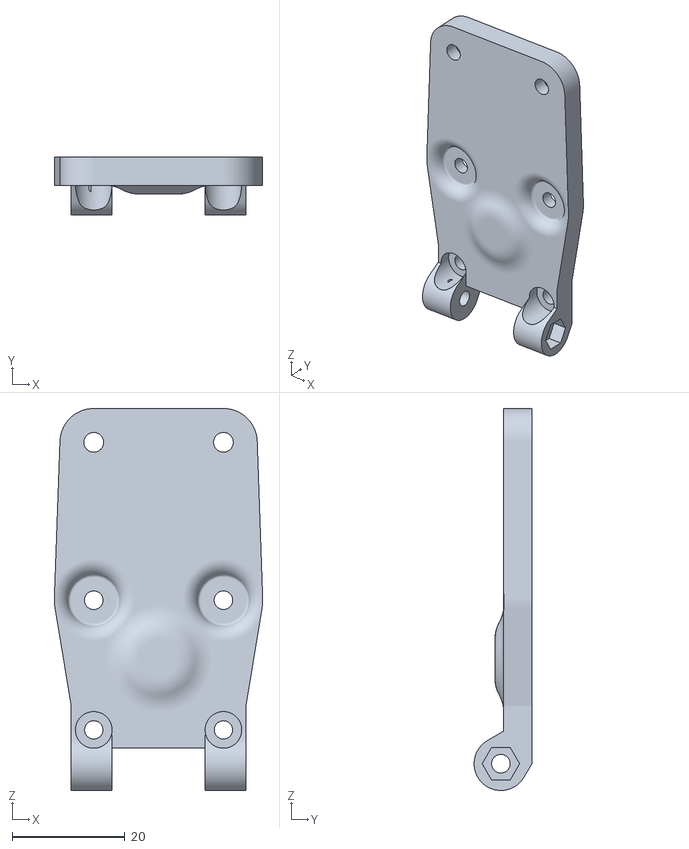
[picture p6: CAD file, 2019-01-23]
3D_Models/3D_Printed_Parts/Printer_Mounts/Prusa_i3_and_Clones/Fulcrum_20mm.stl
37.0 x 10.2 x 67.7

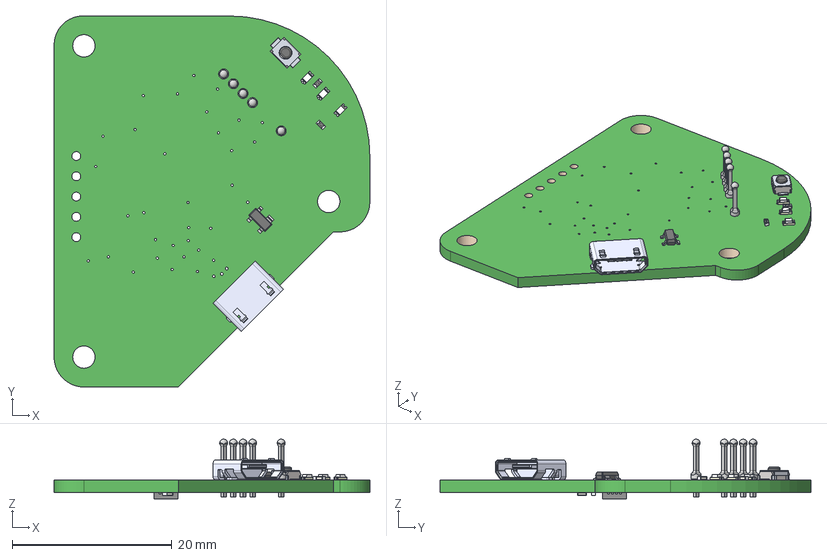
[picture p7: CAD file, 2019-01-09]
3D_Models/Board_Reference_Models/Extruder_Board_programmer.step
39.6 x 46.5 x 7.49 mm
Board
SEEED-LED_LED-0603 x 3
47K x 4
QFN-16 (3x3) Part1
QFN-16 (3x3) Part2 x 16
SP0503BAHTG
10118192-0001LF
SEEED-SWITCH_SW2-2.6-3.0X2.5X1.2+0.4MM
TP x 5

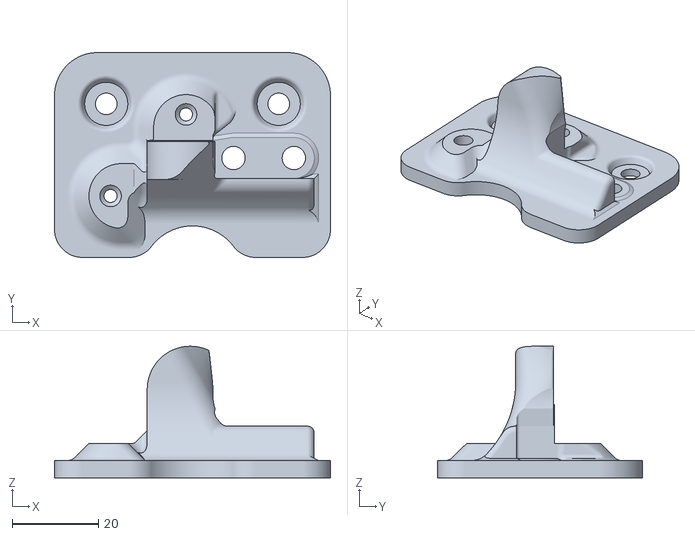
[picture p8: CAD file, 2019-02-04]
3D_Models/3D_Printed_Parts/Printer_Mounts/Creality_Series/Creality-Piezo-Plate-Mount.stl
64.0 x 47.5 x 30.5

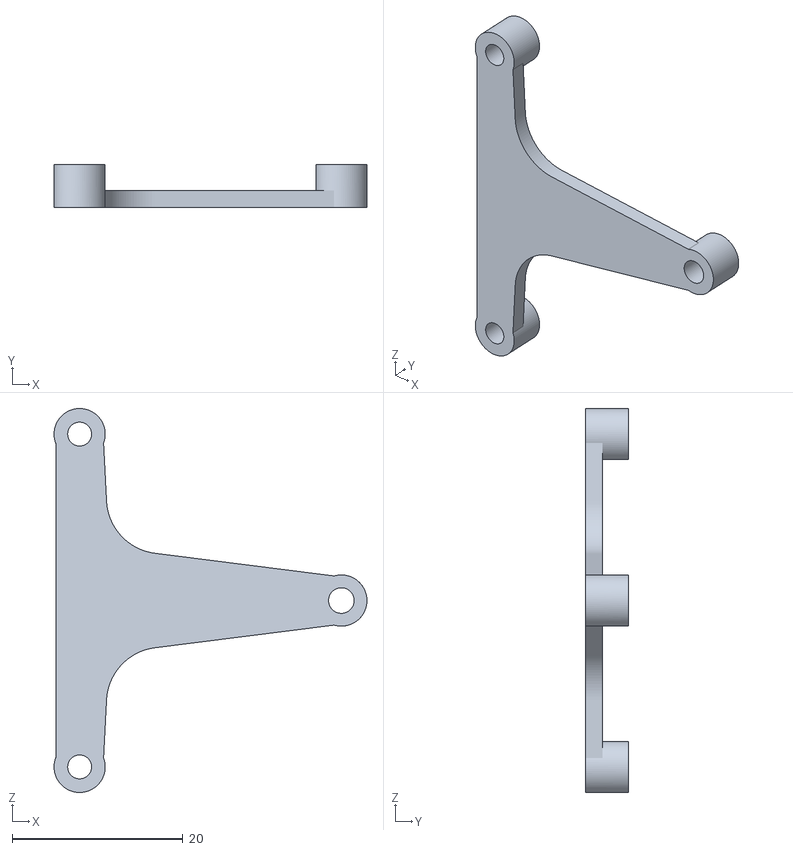
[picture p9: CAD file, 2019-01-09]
3D_Models/3D_Printed_Parts/Printer_Mounts/Prusa_i3_and_Clones/FFC_Board_Mount.stl
36.7 x 5.00 x 45.0

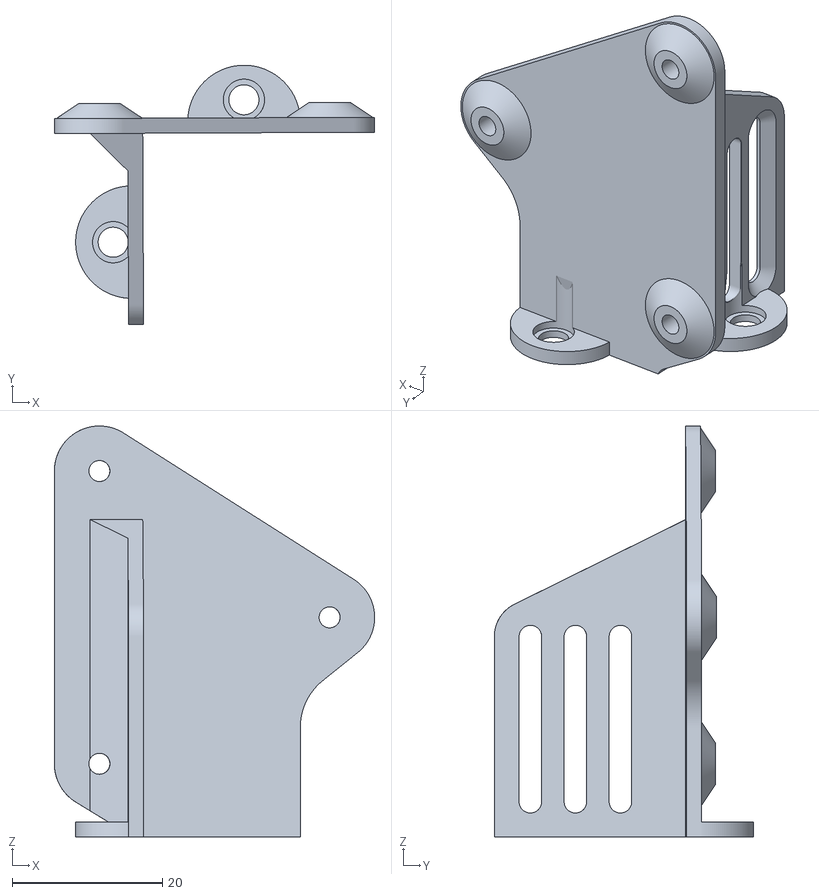
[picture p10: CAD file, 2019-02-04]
3D_Models/3D_Printed_Parts/Printer_Mounts/Creality_Series/Creality-FFC-Board Mount.stl
42.7 x 34.6 x 54.8

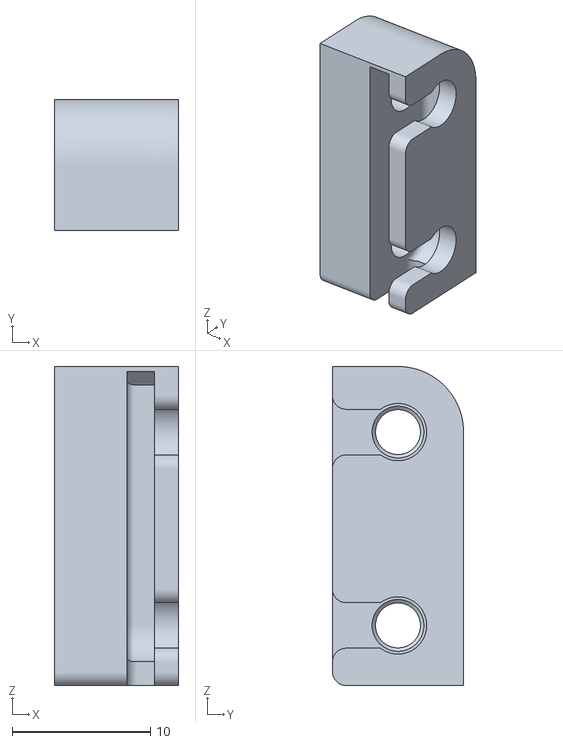
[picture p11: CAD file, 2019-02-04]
3D_Models/3D_Printed_Parts/Printer_Mounts/Creality_Series/Creality-Piezo-Nozzle-Mount.stl
9.00 x 9.50 x 23.1

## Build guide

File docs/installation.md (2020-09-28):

# Pyr0-Piezo Installation Instructions

***Important***: Every printer is different, and this sensor can be adapted to any of them, however we may not currently have a mount designed for your needs. If that's the case, please [open an issue on the github](https://github.com/pyr0ball/pyr0piezo/issues/new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) and/or send us a ping on the discord server.

## Fully Supported Printers

- [Monoprice Delta Mini](tutorials/wiring/easy-piezi/monoprice-delta-mini.md)
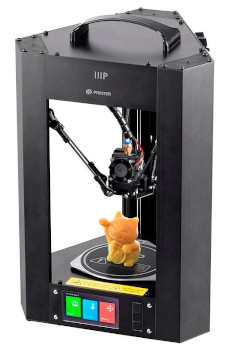
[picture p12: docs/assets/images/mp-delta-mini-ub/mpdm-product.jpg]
  - 

- [Creality Ender 3/5/Pro | CR-10](mounts/creality/creality-original-head.md)
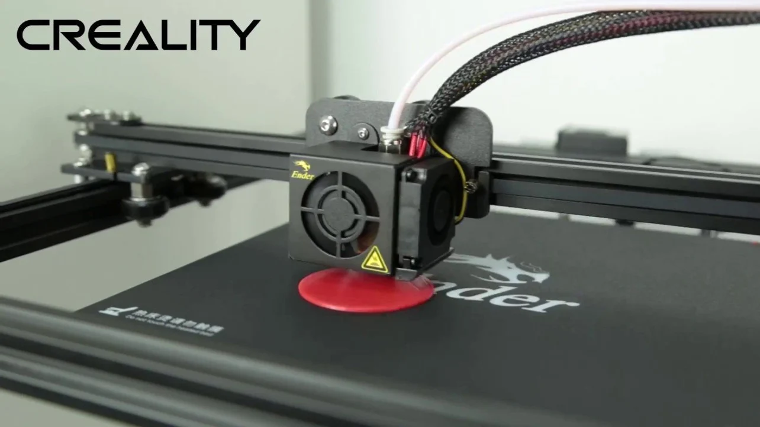
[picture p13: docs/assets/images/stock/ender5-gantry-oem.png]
  - 

## Getting Support for your printer

### Request Support using GitHub

Open a [Printer Mount Request](https://github.com/pyr0ball/pyr0piezo/issues/new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)

### Request Support on Discord

Join the [Discord Server](https://discordapp.com/widget?id=544587989536473099&theme=dark) and request support from pyr0ball#2592

### Choosing your mounting scheme
*First, follow the instructions for physically installing your Pyro-Piezo on the printer you're using:*

- Creality:
  - [CR-10 / Ender 3](mounts/creality/creality-original-head.md)
- Prusa / Mendel
  - [Prusa i3 on Head](mounts/prusa-mendel/i3-on-head.md)
  - [Mendel on Head](mounts/mendel/mendel-on-head.md) | [Mendel Gantry Mount](mounts/mendel/mendel-gantry-mount.md)
- Ultimaker Kinematics
  - [Ultimaker Under Bed](mounts/quadrap/um-under-bed.md)
  - [Makerbot Under Bed](mounts/quadrap/makerbot-under-bed.md)
- Core-XY
  - [Hypercube Evo on Head](mounts/core-xy/hevo-on-head.md)
  - [Railcore II Under Bed](mounts/core-xy/railcore-ii.md)
- Delta
  - [Monoprice Delta Mini](mounts/delta/delta-under-bed.md)
  - [Folgertech Delta](mounts/delta/delta-head.md)
- Deltesian
  - [Bornity's Deltesian](mounts/deltesian/deltesian.md)

## Configuring your Printer/Firmware

[Configuring Marlin to use Pyr0-Piezo](tutorials/config/printer-firmware/marlin/marlin-config.md)

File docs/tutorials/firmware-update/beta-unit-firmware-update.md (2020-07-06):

# Pyr0-piezo Beta Unit Firmware Update Procedure

## Utilizing the Pyr0-Piezo AVR Programming Jig

### Physical Construction of the Jig

The AVR Programming jig consists of several components:

- A PCB with USB-UART bridge (or a TTL header)
- A second PCB with ICSP header and Diag Headers installed
- 5MM 3D Printed Standoffs between the two boards
- 0.65mm Diameter Pogo Pins that span the two PCB's
- The three main body components of the jig
- The hinge joints, and clamp
- Hardware:
  - 4x M3 16mm Bolts
  - 5x M3 22mm Bolts

Assembly animation:

<div style='position:relative; padding-bottom:calc(75.00% + 44px)'>
  <iframe src='https://gfycat.com/ifr/AnimatedInsistentChimpanzee' frameborder='0' scrolling='no' width='100%' height='100%' style='position:absolute;top:0;left:0;' allowfullscreen>
  </iframe>
</div>

---

## Uploading Firmware Without a Jig

Uploading firmware without a Pyr0-Piezo AVR Programming Jig requires soldering to the test pads on the bottom of the Sensor's PCB:

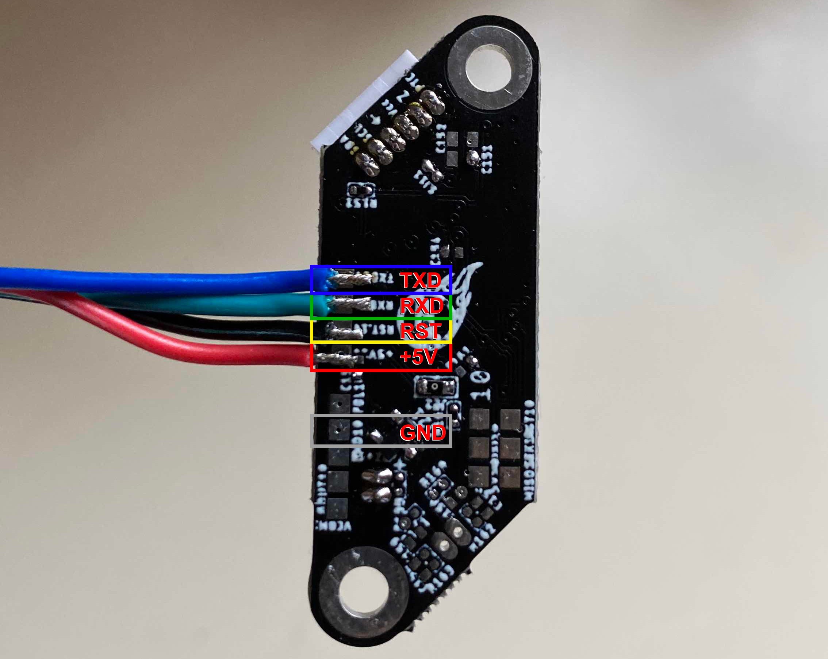
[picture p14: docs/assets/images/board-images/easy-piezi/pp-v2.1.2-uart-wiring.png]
EasyPiezi UART Wiring


To utilize the UART's in-built auto-reset function, a 10k resistor and a small capacitor must be added to the reset wire in the configuration below:

<object data="../../../schematics/other/USB-UART-Wiring-Example.pdf" type="application/pdf" width="100%" height="450px">
    <embed src="../../../schematics/other/USB-UART-Wiring-Example.pdf">
        <p>This browser does not support PDFs. Please download the PDF to view it: <a href="../../../schematics/other/USB-UART-Wiring-Example.pdf">Download PDF</a>.</p>
    </embed>
</object>

---

## Obtaining the Latest Firmware

You can obtain the latest firmware release for this project [HERE](https://github.com/pyr0ball/pyr0piezo/releases/latest) as a zip file with the source, as well as a pre-compiled hex file for use with certain programmers.

---

## Firmware Upload Procedure

The firmware for this project can be updated using one of three methods: VS Code, Arduino IDE, or avrdude.

Please be sure you've already [wired up your sensor's UART port](../../schematics/other/uart-programmer-wiring.md) or used the programmig jig described earlier in this page.

If you built your own board and are starting out with a completely factory-fresh MCU, you'll need to install a bootloader. Have a look at [Uploading over ICSP](https://docs.pyroballpcbs.com/tutorials/firmware-update/beta-unit-firmware-update/#uploading-over-icsp) for instructions on how to do that.

---

### VS Code (Preferred Application)

#### Installing dependencies

1. Install [VS Code from Micosoft's official page](https://code.visualstudio.com/download)
2. Use the "Extensions" menu to install PlatformIO.
3. (Optional) Install extra plugins to assist in development:

- GitLens
- markdownlint
- Markdown Preview Enhanced
- C/C++
- C++ Intellisense
- Python

#### Configuration

1. In PIO Home, open the firmware folder: `~/pyr0piezo/firmware/AVR-Source/Pyr0_Piezo_sensor_v2.x.x`
2. By default, VSCode is configured to utilize the Atmega328PB MCU. This can be changed by editing the `default_envs` parameter in the `platformio.ini` file

#### Upload

1. Make any desired adjustments to default values in `src/pP_config.h`
2. Click the "PlatformIO: Upload" button found in the bottom bar of the VS Code window
3. Verify Serial connection by opening the Serial Monitor and typing `CONFIG` or `STATE`. You should get a response.

#### Uploading over ICSP

Using this method will install the bootloader required to upload firmware over UART

1. Open the `platformio.ini` file found in the Pyr0_Piezo_sensor_v2.x.x folder
2. Change the `defailt_envs` parameter to `ICSP_Bootloader`

```ini
[platformio]
default_envs = ICSP_Bootloader
```

---

### Arduino IDE

1. Install [Arduino IDE from Arduino's official page](https://www.arduino.cc/en/main/software)
2. Under File > Preferences > Additional Board Manager URL's, Add:
    - `https://mcudude.github.io/MiniCore/package_MCUdude_MiniCore_index.json`

---

### AVRDUDESS

#### Windows (Only)

AVRDUDESS is a GUI version of the avrdude application used for flashing firmware to AVR based MCU's, [and can be found here](https://blog.zakkemble.net/avrdudess-a-gui-for-avrdude/)

After installing AVRDUDESS, and opening it, follow the image below with the settings here:

- **A.** Choose the COM port of your UART programmer from the pulldown menu
- **B.** Ensure "Erase Flash and EEPROM" is checked
- **C.** From the MCU Pulldown, select "Atmega328PB"
- **D.** Set the Fuse Bits to `E2`, `DF`, `F9` respectively. Leave LB *blank*
- **E.** Click the Flash button to begin the upload process

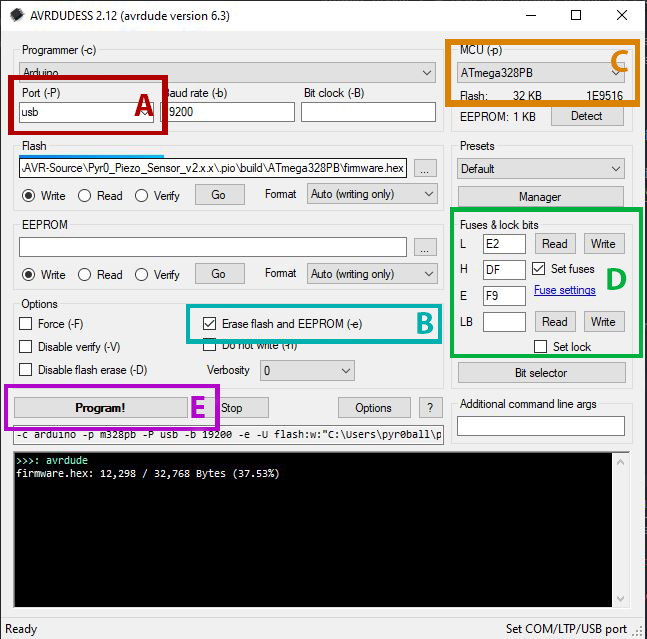
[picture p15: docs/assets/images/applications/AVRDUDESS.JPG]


---

### avrdude

#### Windows

1. Install a bash-like terminal. Choose from a number of options:
    - [Windows Subsystem for Linux]
    - [CygWin]
    - [Mingw64]
    - [Git Bash (Comes bundled with Git for Windows)]
2. Download the [avrdude binaries]
3. Extract the binaries somewhere your terminal can find them

#### Linux

##### Ubuntu/Debian Distro's

```bash
sudo apt update && sudo apt install -y avrdude
```

##### Fedora/RHEL/CentOS Distros

```bash
sudo yum install -y avrdude
```

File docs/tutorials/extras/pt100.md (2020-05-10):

# PT100 RTD Thermal Sensor Integration

The EasyPiezi (Rev 1.1.x and Rev 2.x.x) utilize an extra amp channel to allow the use of a PT100 RTD Thermal sensor with minimal additional components. The circuit is based on E3D's daughterboard designed for PT100 sensors.

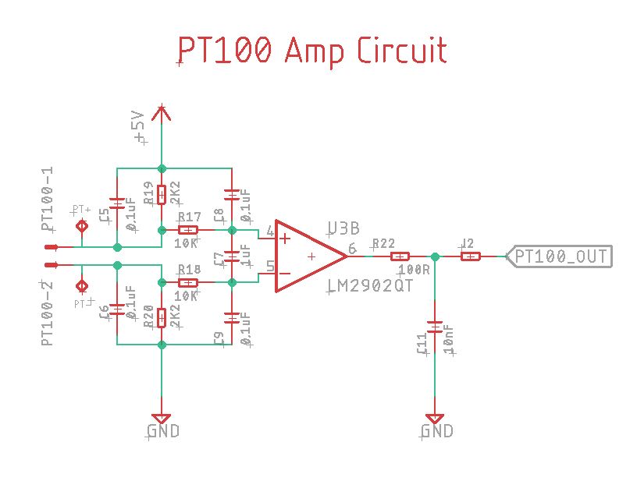
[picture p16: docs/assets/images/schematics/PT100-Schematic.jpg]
PT100-Schematic


The circuit outputs a DC voltage that corresponds to the RTD's change in resistance, which in turn changes based on the temperature of the RTD. This output shares a common ground with other parts of the circuit, so only one additonal output pin is required to utilize it.

As this is a direct voltage reading, the usual TH# inputs on most controllers cannot be used (unless the user removes the pullup resistor attached to the input). Instead, the PT100 input must be attached to a bare analog input pin (any of the pins labeled A##, like A5 on Atmega controllers)

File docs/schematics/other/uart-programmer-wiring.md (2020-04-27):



<object data="../../other/USB-UART-Wiring-Example.pdf" type="application/pdf" width="100%" height="450px">
    <embed src="../../other/USB-UART-Wiring-Example.pdf">
        <p>This browser does not support PDFs. Please download the PDF to view it: <a href="../../other/USB-UART-Wiring-Example.pdf">Download PDF</a>.</p>
    </embed>
</object>

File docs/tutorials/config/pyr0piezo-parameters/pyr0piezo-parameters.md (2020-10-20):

# Settings Reference Guide and Explanation

## Configuring Pyr0-Piezo parameters using serial input

- To change trigger active duration: `TRG_D` [integer for milliseconds]
- To change gain factor: `GAIN_F` [integer for gain state - see note*]
- To change the output logic: `LOGIC [0|1]` (0 for active low, 1 for active high)
- To enable piezo plugged detection: `PZDET [0|1]` (0 for disabled, 1 for enabled)
- To set the sensor logic output voltage: `SIGVOL [0|1]` (0 for 3.3v, 1 for 5v)
- To change ADC hysteresis value: `HYST` [integer in millivolts]
- To change sensor input pullup vRef low threshold: `VFOL` [integer in millivolts]
- To change comparator trigger high threshold: `VCOMP` [integer in millivolts]
- To change the duration between ADC measurements: `LOOP_D` [integer in milliseconds]
- To update the internal vRef constant value **(see notes below): `CONST` [long value]
- To update the internal vRef using a multimeter reading: `ADJUSTVCC` [integer in millivolts]

You can also enable or disable DEBUG output with: `DEBUG [0|1]`

You can query the current configuration with: `CONFIG`

You can query the current state (including ADC measurements) with: `STATE`

To set all settings to defaults, use: `ERASE`

These commands should be wrapped in this format:
> `CMD INT`

Examples:

`GAIN_F 3` <~ set gain factor to index 3 (6x)

`VFOL 2350` <~ set the vref floor to 2.35V

`DEBUG 1` <~ Enable debug output

`STATE` <~ display current sensor status

### *Note for Gain Factor:

The gain STATE is representative of these values:

```
0 = 3x
1 = 3.5x
2 = 4.33x
3 = 6x
4 = 11x
```

### **Note for calibrating internal 1.1v vRef:

The ADC reading function assumes an "ideal" multiplier constant. Each Atmega
chip is slightly different, so it won't be completely accurate without tuning.
Most of the time this won't be necessary, so don't mess with this if you don't
know what you're doing!
The reading can be fine-tuned manually by using a multimeter, and this equation:

`scale_constant = internal1.1Ref * 1023 * 1000`

where

`internal1.1Ref = 1.1 * Vcc1 (per voltmeter) / Vcc2 (per readVcc() function)`

If the scale_constant calculated is different from the default 1125300, update the voltMeterConstant variable in pP_config.h with the correct value or send a new value with `CONST`

Alternatively, you can input a direct reading from a multimeter, in millivolts, and have the sensor calculate the constant value automatically by using `VCCADJUST`

## Sensitivity Tuning Workflow

If you find your Pyr0-Piezo sensor is not triggering as expected, there are several settings that can be adjusted.

### GAIN_F

The first setting that should be adjusted is always the GAIN of the circuit. That is, the amount of amplification the input signal gets multiplied by. Increasing this setting will increase sensitivity, but will also increase noise. If this parameter is set too high, the sensor will likely trigger constantly, or each tap of the piezo will cause multiple or prolonged trigger events.

### VCOMP

After adjusting the GAIN, the next setting that should be adjusted is the voltage comparator threshold. This setting is representative of the "level" that the signal from the piezo must reach in order to produce a trigger event. Lowering this setting will increase sensitivity, as the signal needed to trigger is reduced. Having this parameter set too low will have similar behavior to `GAIN_F` being set too high. If this parameter is set too high, the sensitivity may be reduced too much, or it may not trigger at all. If this parameter is set higher than the input voltage of the circuit, the sensor will report an error and may not function properly.

### VFOL

The Voltage Follower parameter is used as a combination of noise filter and "virtual ground". **This setting must never exceed the parameter set for `VCOMP` as this would cause a constant triggered state. Setting this parameter close to the `VCOMP` value will increase sensitivity, and lowering this parameter will reduce sensitivity but will also reduce noise filtration.

### Best Practices (so far)

`GAIN_F` should be set as high as possible without false triggering

`VCOMP` should be set to 50-75% of the input voltage of the circuit in most cases

`VFOL` may work better higher or lower depending on the environment of the sensor, but higher will filter out more noise and increase sensitivity

## Pyr0-Piezo circuit explanation

In order to understand what each parameter does, a basic understanding of the circuit and signal involved is required.

To begin, we start with the piezo element itself, which usually consists of a disk of brass doped with a piezoelectric ceramic. When flexed, bent, or pressed, this disk outputs a voltage. The amount of energy produced is small, however, and can be "noisy". Each stage of the circuit addresses a different aspect of amplifying, filtering, and conditioning the signal to reject false positives and noise.

## Stage 1: Amplification

The piezo's output is tied to a high impedance input of an [Operational Amplifier](https://www.electronics-tutorials.ws/opamp/opamp_1.html). The Amp stage takes the signal from the piezo and increases it's voltage by a factor, anywhere between 3x and 11x depending on the `GAIN_F` setting. This amplified signal is then passed through to the third stage. The wire between Stage 1 and Stage 3 is also attached to the output of Stage 2 through a high-ohmage resistor. Adjusting the `GAIN_F` setting is the coarsest and easiest way to adjust the sensor's sensitivity.

Use cases for adjusting `GAIN_F`:

 - Sensor is not sensitive enough, or is too sensitive
 - Many false triggers during movement

[Image placeholder. Add a visual of before/after amplification stage]

## Stage 2: Noise Filter & Slow-Recovery Sustain (Voltage Follower)

This stage utilizes a combination of a PWM-based DAC, another Amp channel, and a high-ohmage resistor. The purpose of this stage is to provide a "Voltage Floor" or a "Virtual Ground" to the Low-Side input of Stage 3. This stage is governed by the `VFOL` setting. The essential effect of this stage is that any signal input from the first stage that falls below the `VFOL` threshold will be filtered out and suppressed. This setting can be used to address a noisy input signal from too much EMI, static electricity, or other factors.

Use case for adjusting `VFOL`:

 - Many false triggers when stationary
 - Many false triggers during movement

[Image placeholder. Add a visual of VFol compared to input signal]

## Stage 3: Comparator Trigger

This stage of the circuit utilized another PWM-based DAC to set a "trigger threshold", which is governed by the `VCOMP` setting. When the input signal from the previous two stages increases beyond the threshold set by `VCOMP`, the sensor's Z-Min signal is tripped and a Z-Min trigger signal is sent to the control board of the 3D Printer. As the Follower's filtering signal is attached to this input through a high-ohmage resistor, the amount of time it takes for this triggering circuit to reset is extended, which further reduces multiple trigger signals from being sent. By default, `VCOMP` is set to 2.85v which should be compatible with even 3.3v systems, but there could be instances where the `VCOMP` setting is higher than what the rest of the circuit can provide, and therefore no triggering would occur, even with valid input.

Use case for adjusting `VCOMP`:

 - No triggering from the sensor at all
 - Low input voltage

[Image placeholder. Add a visual representation of the comparator signals]

## Other Settings

**Trigger Duration**

The Trigger duration, governed by the `TRG_D` setting, determines the length of the pulse sent to the printer's control board. Too short of a signal might not be registered by the controller, but too long can interfere with the ADC calculations of the sensor's firmware.

**Loop Duration**

The Loop duration, governed by the `LOOP_D` setting, determines how long the controller waits between ADC readings which are used to automatically balance the circuit. This setting should be kept as short as possible for the best possible results, but too short could cause hitching or overloading of the software.

**Software Hysteresis**

The hysteresis value, governed by the `HYST` setting, is a variable used in the ADC calculation to determine whether to adjust the PWM-DAC duty cycle. The hysteresis value adds or subtracts that value from the ADC comparator calculation. It gives a buffer to the software, preventing it from making adjustments to the DAC outputs below the value defined by `HYST`.

**Volt Meter Multiplier Constant**

The section below is still relevant, but the process for adjusting this setting is now simplified. Simply take a voltmeter measurement from the output of the regulator (or the side of the Zener Diode with the line across it) and input the measurement with `VCCADJUST`

Example:

Measured input voltage is 5.12v

```serial
VCCADJUST 5120
```

The Voltage Multiplier Constant, governed by the `CONST` setting, is a value used in the software to accurately determine the microcontroller's input voltage. However, due to minor differences in each chip, this value may not be completely accurate for each individual board. Usually the amount of difference is so minor as to not make much of a difference, but if desired, the end-user can adjust this constant value by using the following:

`scale_constant = internal1.1Ref * 1023 * 1000`

where

`internal1.1Ref = 1.1 * Vcc1 (per voltmeter) / Vcc2 (per readVcc() function)`

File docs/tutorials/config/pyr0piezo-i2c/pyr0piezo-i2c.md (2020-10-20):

# Integration using I2C

Default I2C Address: **0x10**

## I2C Command Register Map

see [Pyr0-Piezo Parameters Explanation](../pyr0piezo-parameters/pyr0piezo-parameters.md) for more specific details on the command aliases.

|I2C Register|Command Alias|Arguments|Type|Bytes Length
|---|---|---|---|---|
|0x00|GAIN_F|Gain Factor|Input|2
|0x01|VFOL|Millivolts|Input|2
|0x02|VCOMP|Millivolts|Input|2
|0x03|LOOP_D|Milliseconds|Input|2
|0x04|TRG_D|Milliseconds|Input|2
|0x05|HYST|Millivolts|Input|2
|0x06|LOGIC|Boolean|Input|2
|0x07|PZDET|Boolean|Input|2
|0x08|CONST|Millivolts|Input|4
|0x09|CONFIG|None|Output|32
|0x0a|ERASE|None|Input|1
|0x0b|STATE|None|Output|10
|0x0c|SIGVOL|Boolean|Input|1
|0x0d|VCCADJUST|Millivolts|Input|2

## I2C Command Syntax

I2C input syntax uses "Least Significant Byte First" formatting, which means the data bytes are sent in reverse order:

```serial
[Address Byte] [Command Byte] [Data 8] ... [Data 0]
```

For example, to set the Logic output to Active Low:

```serial
0x10 0x06 0x00
```

Or to set VCOMP to 2650:

```serial
0x10 0x02 0x5A 0x0A
```

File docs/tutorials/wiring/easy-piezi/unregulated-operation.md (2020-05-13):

# Unregulated Power Operation with the EasyPiezi

The input voltage regulator built into the EasyPiezi module has a rated input voltage range from **6V and 40V**. There may be some installations that require providing only 3.3V or 5V operation. This is still possible with the EasyPiezi, but requires bridging two pads with solder or conductive tape. This Bypass Solder Brige is labeled SJ1 on the bottom of the board, and can be seen highlighted in the below image:

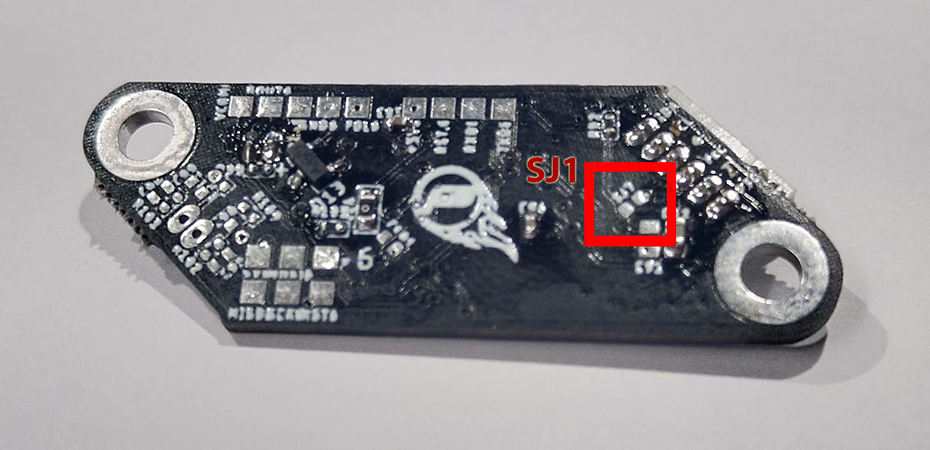
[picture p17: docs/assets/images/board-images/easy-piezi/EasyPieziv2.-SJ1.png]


Simply add some solder between the two pads of SJ1 to bypass the input regulator.

---

## Safety precaution for Unregulated Operation

Bypassing the regulator comes with certain risks. Please be aware that operating the sensor in this mode effectively disables the majority of overvoltage protection built into this device. It's recommmended to add a 10-22uF electrolytic capacitor to the wiring harness between the power and ground terminals to reduce the liklihood of an overvoltage spike that would cause damage to the sensor. Any sustained input voltage above 5.2V will irrepairably damage the sensor module.

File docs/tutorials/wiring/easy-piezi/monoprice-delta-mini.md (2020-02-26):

# Monoprice Delta Mini Installation Guide

## Kit Contents

- 1x Pyr0-Piezo Easy-Piezi Board
- 1x MPDM Cable Harness
- 1x 20mm Piezo Array with adhesive tape

---

## Installing the Piezo Array

1. Remove the six M3 screws securing the bottom cover of the printer, and move the cover to the side.
2. Unplug the fan attached to the bottom cover (This is the Controller Fan).
3. Find and unplug the two cables that go through the hole in the center of the printer's baseplate. These are attached to the heated bed.
4. Rotate the three levers holding the heated bed corners to the side. This will release the heated bed, and allow you to lift the bed off the printer's base. Make sure not to tangle the heater wire's clip in other wires while pulling the bed out.
5. Place the bed top down on a flat surface.
6. One at a time, peel the blue film off the adhesive strip for one piezo disk, and stick it to the bottom of the bed next to one of the posts at each corner of the bed. Make sure to orient the wires so that they are pointed at the center of the bed. Try to place the disk as close to the post as possible without allowing them to touch. Repeat this process for each of the three piezo disks.
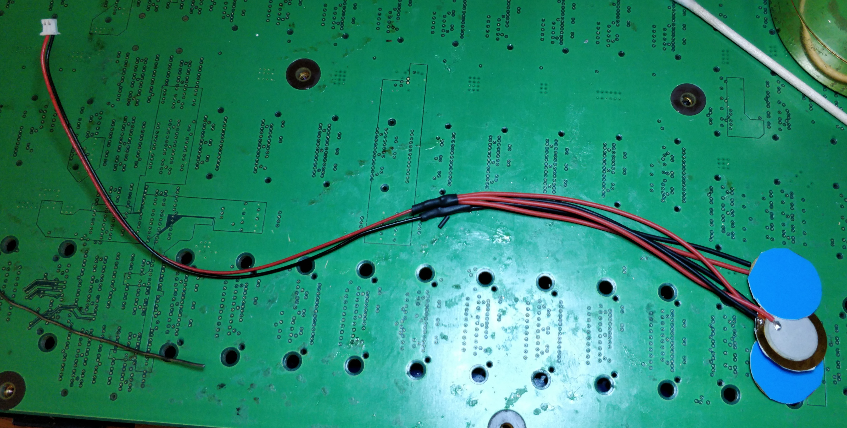
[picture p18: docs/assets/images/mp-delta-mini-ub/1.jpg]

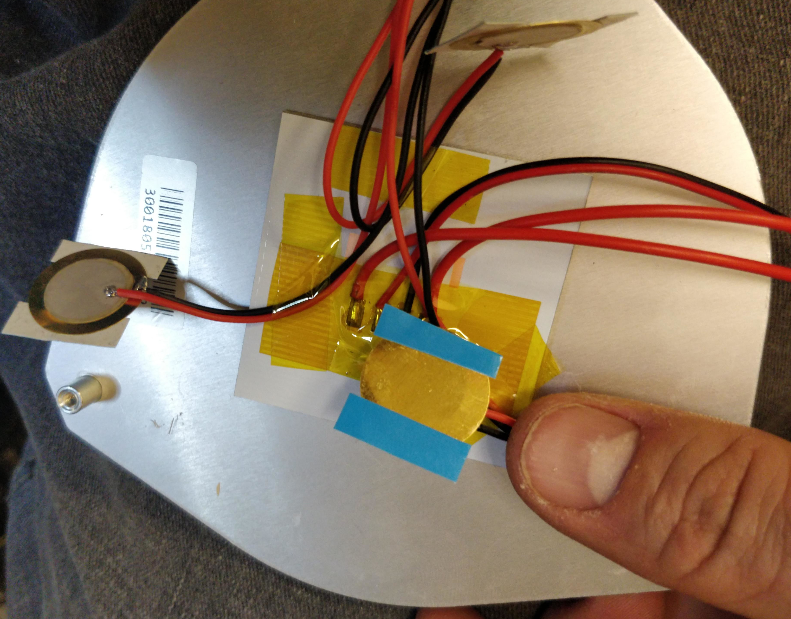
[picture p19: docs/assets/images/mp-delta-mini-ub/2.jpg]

7. (Optional) Using some Kapton tape or other heat resistant adhesive, stick the three wires from the disks to the center of the bed heater. This will make it easier to keep the cables from getting snarled later.
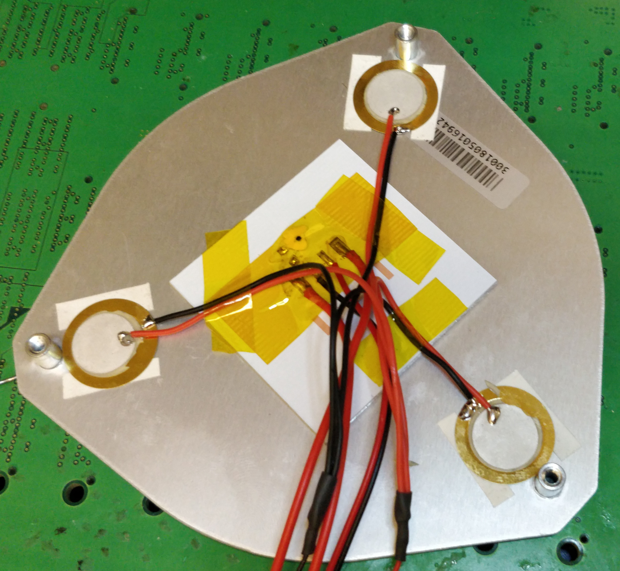
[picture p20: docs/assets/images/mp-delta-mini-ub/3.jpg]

8. Route the wires from the bed back through the hole in the base of the printer, and place the bed back on it's posts. Then rotate the retaining levers back into place. While performing this action, make sure the wires do not become trapped between the bed and the base, but instead hang freely on the inside compartment of the printer.
9. Plug the bed's cables back into the controller, and allow the piezo array cable to hang free for now

## Installing the Easy-Piezi Sensor

1. Disconnect all three Blue/Red wires from the three connectors on the left side of the board (Far side away from the heatsink)
2. Connect the 6-pin connector of the wiring harness (only 3 pins have wires), to the Easy Piezi main connector
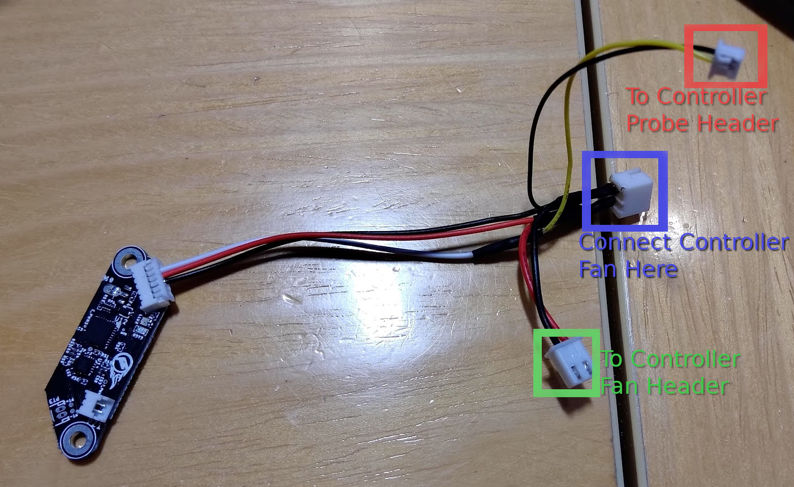
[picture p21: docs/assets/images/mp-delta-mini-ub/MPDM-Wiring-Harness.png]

3. Connect the 2-pin connector from the Piezo Array to the PZ1 2-pin connector on the long side of the Easy-Piezi board
4. Connect the 3-Pin wire from the cable harness to any one of the three now empty connectors from the first step (depicted in Red below)
5. Connect the 2-Pin Power Connector (depicted in Green below) to the Controller Fan header (also depicted in Green below)
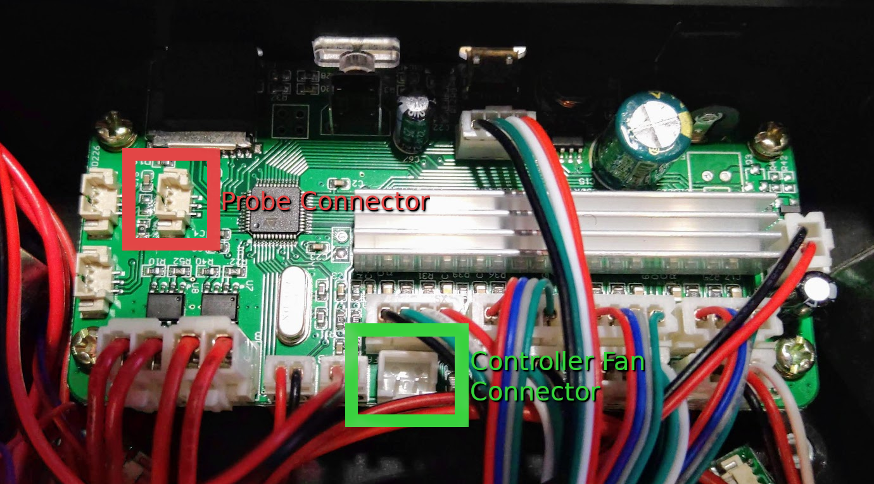
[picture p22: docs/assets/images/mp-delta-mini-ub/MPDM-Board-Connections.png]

6. Tuck the sensor behind the cables to keep it out of the way of the fan.
7. Connect the Controller fan (attached to the base cover) to the Fan Header on the wiring harness (depicted in Blue below).
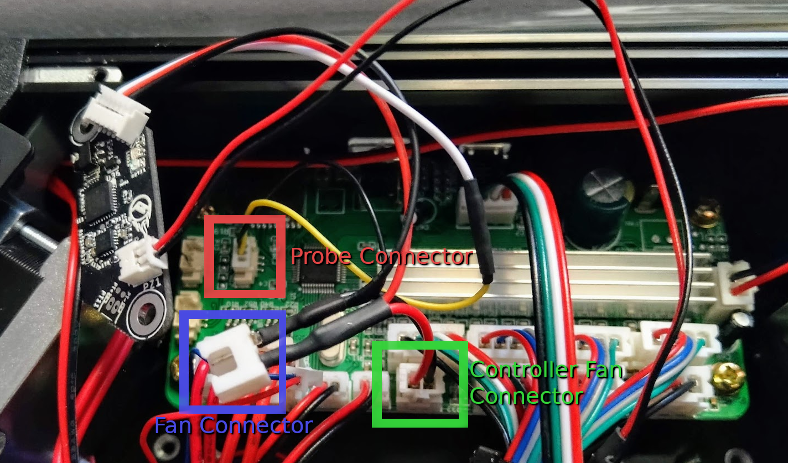
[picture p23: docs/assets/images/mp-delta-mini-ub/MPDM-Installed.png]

8. Re-install the base cover and use the six M3 bolts to secure it.

## Utilizing the Easy-Piezi

### Recommended Pyr0-Piezo settings

```GCODE
GAIN_F 2 ;(4.33x)
VFOL 900
VCOMP 1900
LOOP_D 50
TRG_D 100
HYST 20
LOGIC 0
PZDET 0
```

### G-Code Startup Scripts

By default, most of the slicer profiles available for this printer use a minimal bed leveling approach, using only four test points. As this sensor has enhanced capabilities compared with the default switches, it is beneficial to use a higher number of probe points. This can be done witout modifying the printer's firmware, by simply changing the startup bed leveling command:

```GCODE
; Original:
G29

; Recommended:
G29 P5
```

### Update Web Interface

An enhanced web interface is available from GitHub user [nokemono42](https://github.com/nokemono42) that incorporates all of the available probe density options.



This can be installed by following the instructions found on the [Github Project Page](https://github.com/nokemono42/MP-Mini-Delta-Web)













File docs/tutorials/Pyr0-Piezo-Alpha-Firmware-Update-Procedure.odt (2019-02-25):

# Pyr0-Piezo MCU Update Procedure

Tools and components:

- Pyr0-Piezo Unit
- USB-UART bridge ~or~ Pyr0-Piezo Program Interface Board
- ICSP Programmer or ArduinoISP
- Soldering Iron
- Wire
- 10K resistor
- 100pF – 0.1uF Capacitor (ceramic is preferred)
- Arduino IDE (optional)
- avrdude
- MCUDude's MiniCore
- Pyr0-Piezo git project

Links:

Arduino IDE: https://www.arduino.cc/en/main/software

avrdude: https://download.savannah.gnu.org/releases/avrdude/

Pyr0-Piezo GitHib: https://github.com/pyr0ball/pyr0piezo

Hookup:

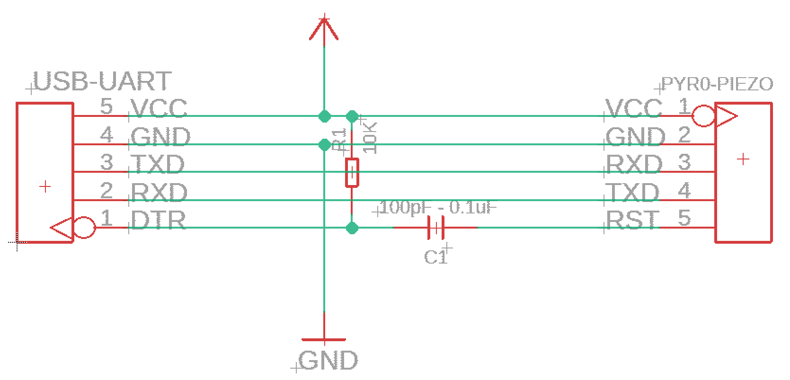
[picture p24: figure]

In order for serial (UART) programming to work, a capacitor must be placed in line between the Pyr0-Piezo RST pin, and the UART's DTR pin, and a 10k pullup resistor between DTR and +5v. ICSP programming requires no extra passive components. TXD/RXD pairs are inverted between sender and receiver

Programming With Arduino IDE

- Download and install the Arduino IDE, clone or download the Pyr0-Piezo project (git clone is recommended to ensure updates are pulled) to a folder of your choosing.
- Open firmware/AVR-Source/ and open the firmware ino file related to the board you're updating.
- Install MCUDude's MiniCore
  - Open File > Preferences, and add the MiniCore json to the “Additional Board Manager URL's” Field: https://mcudude.github.io/MiniCore/package_MCUdude_MiniCore_index.json
  - Click on Tools > Board > Boards Manager, use the search box to find “MiniCore”, and click the “install” button
- Choose the MCU used in your sensor
  - Click on Tools > Board > Select Atmega88 for Rev.1.x.x boards, Atmega328 for Rev.2+ boards. All other settings will be the same
  - Under Tools, set the following:
    - Bootloader: Yes
    - Clock: 8Mhz Internal
    - BOD: anything 2.7v or lower
    - Compiler LTO: Disabled
    - Variant: *8P/PA
- Set the programmer type to Programmer: AVRISP mkII
- Choose the COM port of your USB-UART bridge
- Make any adjustments to the top section of variables
- Click on “upload”
- Done!

Programming with avrdude

- Download avrdude (or find avrdude installed along with ArduinoIDE: Arduino/hardware/tools/avr/bin) and extract it to a folder of your choosing.
- Copy the firmware for your board out of /firmware/Compiled-Firmware/*.hex to the folder where you extracted avrdude
- run the following command, replacing the m88p with m328p if using a Rev.2+, and COM4 with the serial port of your USB-UART bridge

./avrdude.exe -c avrisp2 -p m88p -b19200 -PCOM4 -U flash:w:<firmware.filename>.hex -v

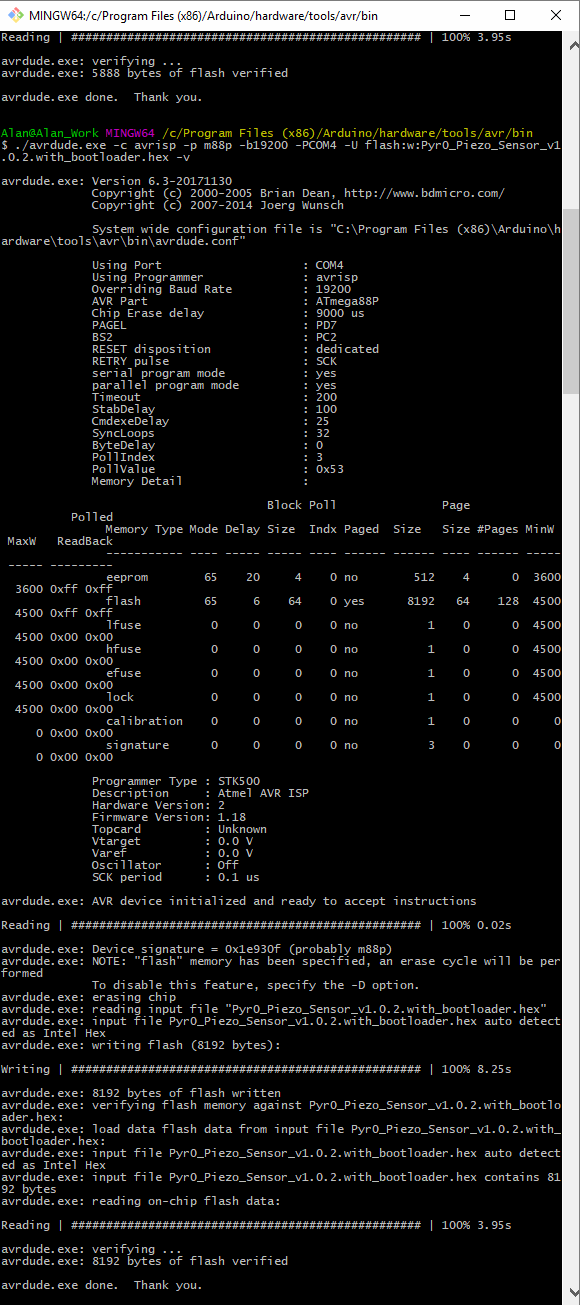
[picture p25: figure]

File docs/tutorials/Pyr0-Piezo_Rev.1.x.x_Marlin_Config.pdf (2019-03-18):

## Pyr0-Piezo Z-Probe rev.1.x.x Marlin Config

Most mechanical endstops use “active low” logic, which requires Marlin to be configured for endstop pins to be pulled up, and the default logic to be inverted.

This methodology has been adopted as of Rev.1.0.2. All pyr0-piezo sensors will use active-low logic:

Step1 – Endstop Settings:
Comment #define ENDSTOPPULLUP_ZMIN (or other pin if using a different connection) Set Z_MIN_ENDSTOP_INVERTING to “true”

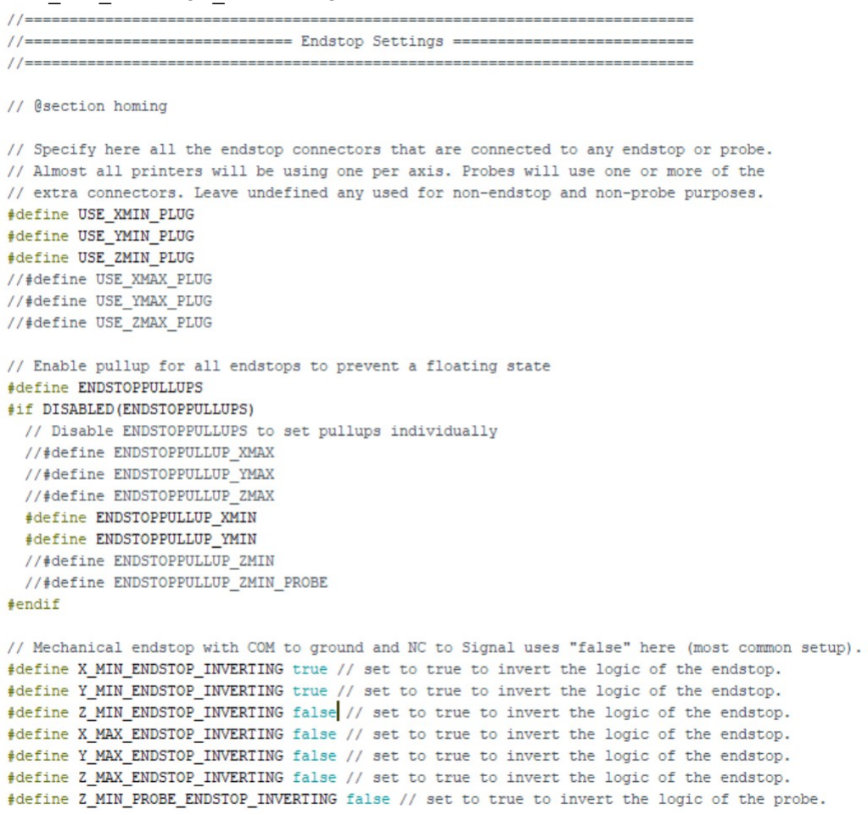
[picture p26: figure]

Step 2 – Enable Interrupts*:

*This only applies if you are running Marlin v1.1.9 or later

Uncomment this line for best possible accuracy

Step 3 – Configure Z Probe Options:
- If using the Z_Min input, uncomment #define Z_MIN_PROBE_USES_Z_MIN_ENDSTOP_PIN
- Uncomment #define FIX_MOUNTED_PROBE
- Uncomment #define PROBING_FANS_OFF
- Uncomment #define DELAY_BEFORE_PROBING 250
- Set all probe offsets to 0
- Change Z_PROBE_SPEED_SLOW to match FAST
- #define Z_PROBE_SPEED_SLOW (Z_PROBE_SPEED_FAST)
- *Optional: Uncomment #define MULTIPLE_PROBING 2
- Uncomment #define Z_MIN_PROBE_REPEATABILITY_TEST
Step 4 – Configure Bed Levelling:
- Choose your flavor of bed leveling and uncomment the line for it. Theoretically Unified Bed Levelling is the best choice for this kind of probe
- *Optional: Uncomment #define RESTORE_LEVELING_AFTER_G28 if you don't plan on doing a full G29 after each G28
- Uncomment and set #define MANUAL_Z_HOME_POS -0.15
- Uncomment #define Z_SAFE_HOMING
- Default for this setting puts the nozzle in the center of the bed for G28Z, but you can define a corner offset if you wish. This will be performed before any bed levelling procedure

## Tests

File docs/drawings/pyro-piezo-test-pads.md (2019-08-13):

Pyr0-Piezo Unified Test Point Platform

<object data="../../drawings/Pyr0-Piezo_FFC_Extruder_Boardv1.1.0_Test_Pads.pdf" type="application/pdf" width="100%" height="450px">
    <embed src="../../drawings/Pyr0-Piezo_FFC_Extruder_Boardv1.1.0_Test_Pads.pdf">
        <p>This browser does not support PDFs. Please download the PDF to view it: <a href="../../drawings/Pyr0-Piezo_FFC_Extruder_Boardv1.1.0_Test_Pads.pdf">Download PDF</a>.</p>
    </embed>
</object>

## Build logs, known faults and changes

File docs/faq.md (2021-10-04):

**Q:** Pyro-Piezo? EasyPiezi? What's the difference?

**A:** Pyr0-Piezo refers to the circuit that utilizes Piezoelectric Elements to perform auto bed leveling on 3d Printers, while the EasyPiezi is a standalone board dedicated to carrying this circuit. The Pyr0-Piezo circuit can be integrated into other boards and designs, such as the Pyr0-Piezo FFC.

---

**Q:** What's the difference between the EasyPiezi and the Pyr0-Piezo FFC?

**A:** The Pyr0-Piezo FFC allows the user to replace their existing bulky cable chain with a [Flexible Flat Cables](https://en.wikipedia.org/wiki/Flexible_flat_cable), while also incorporating the Pyr0-Piezo Z-Probe circuit, fan voltage regulation, motor driver protection diodes, and visual feedback LED's

---

**Q:** Does this sensor support 3.3v logic controllers?

**A:** Yes, if you bought a production (v2.3.0 or later)  board, the logic level of the circuit is configurable to be either 5v or 3.3v. For pre-production (beta) boards, this is possible by following [this guide](tutorials/wiring/easy-piezi/unregulated-operation/)

---

**Q:** Is it required to use the SingleDisk Piezo Adapters?

**A:** No. the SingleDisk adapter board is simply a carrier for a 12mm piezo disk that has the dual benefit of maximizing signal-to-noise ratio, and providing a consistent mounting scheme. All that's required is a piezelectric element that has positive and negative rails that can be connected to the Pyr0-Piezo circuit.

---

**Q:** Will the sensor work if it experiences constant spring pressure?

**A:** Yes! You can even pre-tension the piezo and pick up the "relief" motion if you hook it up backwards

---

**Q:** Why don't you offer drilled piezo disks or use them in your designs?

**A:** You can certainly use drilled disk and make it work with the Pyr0-Piezo, but I don't recommend using drilled discs. You'll get much more consistent results by bending the disk across it's diametric center by allowing one side of the disk to be free moving, and the other statically mounted. The SingleDisk Adapter PCB uses 12mm disks and produces the same signal to noise ratio as a 27mm drilled disk. You can find those [in the shop](https://pyroballpcbs.com/product/pp-singledisk-adapter-pcb/), or you can use the sources in the hardware section of [this repository](https://github.com/pyr0ball/pyr0piezo) to send out to JLC or another fab house if you'd like to build your own.

---

**Q:** How does heat affect the performance and / or lifespan of the sensors?

**A:** Piezo elements have a particular behavior when it comes to heat, which is that their sensitivity is reduced as more heat is applied. That signal degradation is partially elastic, partially plastic. An analogy that fits is bending a piece of wire. If you deflect a copper wire a small amount, it will return to its original shape, which is an "elastic deformation", but if you bend it further, it will stay in it's deflected state, which is a "plastic deformation". The piezo elements' signal output has a similar effect with heat. After a certain temperature, the signal suppression becomes permanent, but below that threshold, it's elastic. That threshold is different between all elements, so you'll have to test with the ones you've got to find out how much heat they can take.

There's a couple of ways do account for this. The Pyr0-Piezo has the ability to increase it's input signal gain on the fly, so even if the signal from your piezo elements is suppressed, it can be boosted by the sensor to a certain extent. It's also possible to increase the gain beyond the 11x limit of the software, but that would require changing a resistor on the board. If your particular setup requires a higher input gain, and you don't want to do your own modifications, I can rework a unit for you upon request.

Another way to address that issue is to migrate the piezo elements to another location that's still mechanically actuated by the nozzle touching the bed, like under the bed mount screws/springs, or by sandwiching an element between the X/Y gantry carriages of the printer.

---

**Q:** Why is center of my print bed leveling differently than the edges?

**A:** Likely the print bed is too flexible, and is bowing during probing. You may need to add a rigid frame, or an additional plate to increase the rigidity of the bed. Combining several piezo elements under the bed, and on the print-head can also partially mitigate this issue.

---

**Q:** Does filament ooze effect my probing?

**A:** It does! Theres a few ways to handle ooze while probing:

- Add a nozzle cleaning routine to your printer's startup behavior (or to the G29/ABL function alone)
- Account for the offset with `Z-OFFSET` in your printer's configuration
- Only probe with the bed at full temperature, and the nozzle below the glass-transition temperature of the filament

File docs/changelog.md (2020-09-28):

# Pyr0-Piezo Changelog
### 551fcb7 to cfa0abc

Changelog updated 2019-08-15_15-31-12

  *Added Features*

------------------------------------

  *Bugfixes*

------------------------------------

  *Full Changelog*

- Initial upload of arduino sketch for the atmega48 [view commit](http://github.com/pyr0ball/pyr0piezo/commit/1e29f10162b43f05fb9b373bdf9d56c5ca3a4a3a)

- added gitignore [view commit](http://github.com/pyr0ball/pyr0piezo/commit/a53b1ff4c5df97346a08022b9bd9e437b08b7cee)

- Added eagle board files [view commit](http://github.com/pyr0ball/pyr0piezo/commit/d7ba9d674c0a7d6f7dfd7ab4f1edb7c4cd662803)

- added mask for temporary eagle files [view commit](http://github.com/pyr0ball/pyr0piezo/commit/beff1d8d1414e4a27143a70c19ced4acd0145df1)

- Initial upload of 3D models [view commit](http://github.com/pyr0ball/pyr0piezo/commit/19aa237fc1edc80658914f440ca2969e93ce0575)

- Updated Readme with links [view commit](http://github.com/pyr0ball/pyr0piezo/commit/54b043ed84963a6b0f2a710a65e74989af748d85)

- Removed debug serial output, fixed voltage reference divisor [view commit](http://github.com/pyr0ball/pyr0piezo/commit/39a01816461d5b4421535330f9cdea1160dbd019)

- Merge branch 'master' of https://github.com/pyr0ball/pyr0piezo [view commit](http://github.com/pyr0ball/pyr0piezo/commit/a2000783fe1b3af648191e2ca3ce42867fcbb7e6)

- Fixed syntax error in voltage adjustment function [view commit](http://github.com/pyr0ball/pyr0piezo/commit/d053b051f47dcac64b485411c264d683c11f5fce)

- Fixed syntax error in Error State function [view commit](http://github.com/pyr0ball/pyr0piezo/commit/5d840f2e7af7913a009c818ec75b8c7bbdc3101b)

- Reduced default loop time, syntax errors were resolved [view commit](http://github.com/pyr0ball/pyr0piezo/commit/a3c0cbbf9813b6a05a98d292fa755a1e7f8ef29e)

- Added comments for PCInt vs Int pin usage [view commit](http://github.com/pyr0ball/pyr0piezo/commit/2e6061d49160c15a0f357bce0c31d429b6cd64e3)

- Moved test points for spi to ICSP standard header [view commit](http://github.com/pyr0ball/pyr0piezo/commit/be4af9fd672ef5c82eade77e2686f4c8548c3156)

- Added bom files for each board [view commit](http://github.com/pyr0ball/pyr0piezo/commit/5d9052de98a9ab3e7284a62a8ff355d12637af98)

- Adjusted placement of text [view commit](http://github.com/pyr0ball/pyr0piezo/commit/9d8dcdcc90c308dbba584660c669293d516a57a5)

- Fixed accidental short of pin to ground [view commit](http://github.com/pyr0ball/pyr0piezo/commit/6b581a53db9eaf6c166a5cd506584dc63abf7f60)

- Adjusted trace placement, added logo to bottom of board [view commit](http://github.com/pyr0ball/pyr0piezo/commit/7514efb97275542b1498e6f5c736ceba249dadfb)

- Updated standalone board with final piezo circuit [view commit](http://github.com/pyr0ball/pyr0piezo/commit/f277063c285ac7836806186993e1f29a44e7a1c7)

- Created separate sketch for smaller flash [view commit](http://github.com/pyr0ball/pyr0piezo/commit/29d8a2565a9eb07b87c0d00b55bd49f96925faeb)

- Begin refactor of sketch for smaller flash footprint [view commit](http://github.com/pyr0ball/pyr0piezo/commit/add37b05f55e45fe65f3a694679c6e5075925081)

- Added description to Eagle project folder [view commit](http://github.com/pyr0ball/pyr0piezo/commit/2f71b9e8cb8ece5b90f57754b90b82588840082e)

- Reorganized 3D models [view commit](http://github.com/pyr0ball/pyr0piezo/commit/21457c0c85fcd83d1e87bae0cf2b2476b0593500)

- updated readme [view commit](http://github.com/pyr0ball/pyr0piezo/commit/530d00f316e8f1e56d9ec69c9d9420fdaa22d1ea)

- Update Readme [view commit](http://github.com/pyr0ball/pyr0piezo/commit/cfa0abcaa5a3fb9236b7c1790dad26d5e9437b02)

### cfa0abc to 76b4ba6

Changelog updated 2019-08-15_15-32-15

  *Added Features*

------------------------------------

  *Bugfixes*

------------------------------------

  *Full Changelog*

- fixed trace accidentally connected to ground [view commit](http://github.com/pyr0ball/pyr0piezo/commit/d2263348f308ccfb95b55bcf3c1cc997aaabb38a)

- Renamed boards, Fixed programmer [view commit](http://github.com/pyr0ball/pyr0piezo/commit/3f6366d8e722d195172192957b1f77d84b6d9227)

- Pulling latest before pushing changes. [view commit](http://github.com/pyr0ball/pyr0piezo/commit/47cd908b0b7c9b9aa0ffd317fe62d6ab79d4326a)

- Rebuilt and corrected mount hole spacing [view commit](http://github.com/pyr0ball/pyr0piezo/commit/3c47f3015003d52ee71ed0fb80dc5d8aa1ab700d)

- Created mounts for stock Creality/Tevo/TronXY extruders [view commit](http://github.com/pyr0ball/pyr0piezo/commit/4a4e316b678f6dd5683fc359e78761ef9165db80)

- Created tolerance cavities for inserting bearings [view commit](http://github.com/pyr0ball/pyr0piezo/commit/7885a101cf0be66efc169e2876df145f5937da05)

- Added tolerance for knurled nut insert [view commit](http://github.com/pyr0ball/pyr0piezo/commit/48914961a3ef1a17d2ce34a14f90c2b6292893c7)

- Added cutout for slide-on nozzle mount to be easily added [view commit](http://github.com/pyr0ball/pyr0piezo/commit/5339a166a2133d3118832b264fdff85dabeb860d)

- Added ICSP Header/breakout to programmer [view commit](http://github.com/pyr0ball/pyr0piezo/commit/1ee75ad0bd589ba02ff089ad4b20a90f95cc070e)

- Added simple overvoltage protection to standalone [view commit](http://github.com/pyr0ball/pyr0piezo/commit/79da9c6468af9ee90bc09aca5c1727b394169f21)

- Added alternate TVS diode [view commit](http://github.com/pyr0ball/pyr0piezo/commit/521b2b6aa50fb90f1e1593bec8eb5b0a50b477f1)

- Fixing Merge conflicts [view commit](http://github.com/pyr0ball/pyr0piezo/commit/7ed11b1003ffb7d9373105577274578c7a6b376d)

- re-adding files after fix-merge [view commit](http://github.com/pyr0ball/pyr0piezo/commit/103cd9ca6abdf87afb0e812f08e5d7808d3e438e)

- Replaced opamps with single quad-channel [view commit](http://github.com/pyr0ball/pyr0piezo/commit/ab1393593435514c0c28993d38444556bd693eeb)

- removed copypasta link [view commit](http://github.com/pyr0ball/pyr0piezo/commit/13c3632f61317565cddbfcb3cc4b10a23e3f010e)

- Fixed airwires and overlaps caused by swapping IC [view commit](http://github.com/pyr0ball/pyr0piezo/commit/60b4da727fcbcf64ba676874b028c9782ab5d5bd)

- Merge branch 'master' of https://github.com/pyr0ball/pyr0piezo [view commit](http://github.com/pyr0ball/pyr0piezo/commit/95230a3df3b04349b6dd0ee5837d3ce2f5be5176)

- re-adding AVR programmer after fixing conflict [view commit](http://github.com/pyr0ball/pyr0piezo/commit/5dadfdec3a81b2738ffd3e2a50d48ffe93ae2e0b)

- Rotated parts to proper printing orientation [view commit](http://github.com/pyr0ball/pyr0piezo/commit/91aa09c1b8f13cba54d6c8edb333901f0904460b)

- added ICSP header for standalone units [view commit](http://github.com/pyr0ball/pyr0piezo/commit/e1ac334c8433dc04e894647bb239a3c8344c3a2c)

- updated with minor fixes to text placement [view commit](http://github.com/pyr0ball/pyr0piezo/commit/c4338f74340dd79a2b85692594197128ea375785)

- fixed missing ziptie channels on prusa mount [view commit](http://github.com/pyr0ball/pyr0piezo/commit/de18f5440f0505ecc662aa1ea9919a51bcb52895)

- Added sources folder for 3D Models [view commit](http://github.com/pyr0ball/pyr0piezo/commit/9d34047d7f7b10474731a32a542c58cb1bf1b73a)

- Added info to readme [view commit](http://github.com/pyr0ball/pyr0piezo/commit/934c763b5cf2cb6f07f4a6c6be44a2d39c97e6a3)

- Update README.md [view commit](http://github.com/pyr0ball/pyr0piezo/commit/d2352b485eba3fe2f87010e5b1e784d3c89f285d)

- moved usb to bottom of board, fixed caps [view commit](http://github.com/pyr0ball/pyr0piezo/commit/8aeef551a6823d0f671bb3861b804d5018e0a187)

- v1.1 Piezo Standalone board [view commit](http://github.com/pyr0ball/pyr0piezo/commit/d51cad7c9f62cb5e1c3f562f2f47c4478f2994e3)

- Added missing 0.1uF cap on AVR Vcc [view commit](http://github.com/pyr0ball/pyr0piezo/commit/76b4ba6de85c22860812434a810aa49c5ef76b0f)

### 76b4ba6 to v2.0.0

Changelog updated 2019-08-15_15-49-28

  *Added Features*

------------------------------------

  *Bugfixes*

------------------------------------

  *Full Changelog*

- Optimized trace layout, serpentined usb [view commit](http://github.com/pyr0ball/pyr0piezo/commit/fcb41c6ceb7d0b257f642a24ec6a98c8cee91f67)

- fixed footprint for LM2902, optimized traces [view commit](http://github.com/pyr0ball/pyr0piezo/commit/0b4e0d56df621e5de7ac43b4e4eb7d8816ab22f7)

- Added version with PT100 amp integrated [view commit](http://github.com/pyr0ball/pyr0piezo/commit/76f6987b55c771b7c4459a42ef5a0f13f37648e0)

- Added labels to controller connector [view commit](http://github.com/pyr0ball/pyr0piezo/commit/45bbd4eba026dfd84acb4bef9ad84a8ac6b2b716)

- Fixed airwires and overlaps [view commit](http://github.com/pyr0ball/pyr0piezo/commit/5ad907556143720329d2de32d452ca724519698d)

- Adjusted spacing on traces/components [view commit](http://github.com/pyr0ball/pyr0piezo/commit/141e0c62e8b62b79ab6ddfc737204051f6fa0a95)

- Fixed spacing for zener diode [view commit](http://github.com/pyr0ball/pyr0piezo/commit/2d7a85786b5f8cbad325b5704f73c0c2cb0cc33a)

- Removed VCC_Reg output smoothing transistor [view commit](http://github.com/pyr0ball/pyr0piezo/commit/cd5d5328b1a011a24ae0c4a9c4348d60304052a6)

- Added Fusion source files for Creality OEM mount [view commit](http://github.com/pyr0ball/pyr0piezo/commit/52fe8d6282ced4f876d74c71ddf91a2bdd1fe5c3)

- Reduced FFC breakout overall size, begin rewire [view commit](http://github.com/pyr0ball/pyr0piezo/commit/b1f61fc386b181846fa754403d76f8ab9859f190)

- Prepare for major rewire (26p -> 60p) [view commit](http://github.com/pyr0ball/pyr0piezo/commit/bc0ab926724c41fcb911675c18b2c8ebee27f6ff)

- Added support channels for upper bearings [view commit](http://github.com/pyr0ball/pyr0piezo/commit/2b30ffffc6519b935a6bae4d5b684a77bd1af553)

- Added folder structure for firmware source [view commit](http://github.com/pyr0ball/pyr0piezo/commit/26f0e138186e1b0100f775e267ac166a6ffd2671)

- Added discord server link [view commit](http://github.com/pyr0ball/pyr0piezo/commit/0373768a64035cc8f1b8a5a269d478246f8fccab)

- Added v2.0.0 Extruder board, rewire for 60p [view commit](http://github.com/pyr0ball/pyr0piezo/commit/118e8cf7e0f64ea669cd7298c0c62c95fe758189)

- Gave some extra space to zener diode [view commit](http://github.com/pyr0ball/pyr0piezo/commit/a695c8e0699c1b3be52387b1bb1dcd69eb15170b)

- Added drawing for Standalone board component layout [view commit](http://github.com/pyr0ball/pyr0piezo/commit/b4a00b77be29cc7c1818e73ea4e3e0f9452c4e70)

- Brought FFC extruder board up to v1.1 spec [view commit](http://github.com/pyr0ball/pyr0piezo/commit/070bef876b96773af2c13c0505ce141b0b537d15)

- Pushing changed files saved after exporting gerber [view commit](http://github.com/pyr0ball/pyr0piezo/commit/3c8372f490568fb7f559dc03fb86434b6d4d484b)

- Modified footprints and added 3D Models for caps [view commit](http://github.com/pyr0ball/pyr0piezo/commit/ba45f8da89e1accc66f7c76d9e38619bc253aeb2)

- Added pinout/hookup drawings [view commit](http://github.com/pyr0ball/pyr0piezo/commit/1d17a8dbc9c0e2c366f647574b28ad20244343db)

- Added drawings and docs for Extruder FFC v1.1.0 [view commit](http://github.com/pyr0ball/pyr0piezo/commit/e2399797b8cc4d5ed9e25f0dfded744ae7c06701)

- Added firmware hex file used in alpha boards [view commit](http://github.com/pyr0ball/pyr0piezo/commit/201ecde19e179790f0cc56eb13285705e985e19d)

- fixed some spacing and labelling [view commit](http://github.com/pyr0ball/pyr0piezo/commit/73c7b875014bc8388a2964834d9ddac2014318a9)

- Rev.2.0.0 - Rewired for full piezo circuit control [view commit](http://github.com/pyr0ball/pyr0piezo/commit/2226025830b979959ceab5072745ae53b767f4f4)

- Corrected naming convention for Standalone 1.0.2 [view commit](http://github.com/pyr0ball/pyr0piezo/commit/6eb53d303982e187e6a0ee912f4152b31a35b99b)

- Exported PDF schematics of all boards that have been fabricated [view commit](http://github.com/pyr0ball/pyr0piezo/commit/c462b0a3dc5661c0f24a280ded8cff5d5fa49069)

- Moved schematics to correct documentation folder [view commit](http://github.com/pyr0ball/pyr0piezo/commit/5bd5e5e99b235e62ae5fdb24db2ca8cc00116cd2)

- Added guide for configuring Marlin on rev.1.x.x [view commit](http://github.com/pyr0ball/pyr0piezo/commit/f377481b7485ebd226bf2b1b6bc84a8421c698e8)

- Swapped/repositioned components [view commit](http://github.com/pyr0ball/pyr0piezo/commit/abd8b9830ecd5373c7f63cbd33d2f17e43949102)

- Minor adjustments to silkscreen and traces [view commit](http://github.com/pyr0ball/pyr0piezo/commit/e5806bd56fba634c56255d70a0613200f90c1b4a)

- Fixed https://github.com/pyr0ball/pyr0piezo/issues/17 [view commit](http://github.com/pyr0ball/pyr0piezo/commit/7fd60d1d74bb22c0714093e4cbdfd659805e22fb)

- First draft of firmware v2.0.0 [view commit](http://github.com/pyr0ball/pyr0piezo/commit/055ab3c09e125308f3f43fd9b9facaeb8a6b9188)

- Added basic serial input to modify parameters [view commit](http://github.com/pyr0ball/pyr0piezo/commit/7999321f8c729364b9f8a20c6c466a62519c9fa9)

- Added the serial input function to the loop [view commit](http://github.com/pyr0ball/pyr0piezo/commit/f9c1e4ff4e89eeef9350cf95b10de53a559d3c47)

- fixed pin assignment from debug edit [view commit](http://github.com/pyr0ball/pyr0piezo/commit/4548a2ed8f2d6a75721dca6b74b991b3172ce781)

- Added test pads for amp circuit debug [view commit](http://github.com/pyr0ball/pyr0piezo/commit/0d31025069fcf20d58444ebe3aa92029129fc10c)

- compiled 1.0.2 firmware with fixed output pins [view commit](http://github.com/pyr0ball/pyr0piezo/commit/ec88e787e99b3309d85bf7af4a126f5d0067b0f1)

- Updated schematic with cleaned up and labelled circuit [view commit](http://github.com/pyr0ball/pyr0piezo/commit/d53aa7f2384a915580ee3389f65c23d3dc653eaa)

- Brought FFC board up to v2.x spec. [view commit](http://github.com/pyr0ball/pyr0piezo/commit/45777727dd5b70a83c56ab72aeeb19427bc068ac)

- Removed cavity behind bearings causing binding [view commit](http://github.com/pyr0ball/pyr0piezo/commit/81c017034029782ec5b5e625477d1569d2b6252f)

- Added X-motor and X-min breakouts [view commit](http://github.com/pyr0ball/pyr0piezo/commit/56ca2af4ac800a9004a3b87f37bda26cdf215b85)

- saved under Eagle v9.3.1 [view commit](http://github.com/pyr0ball/pyr0piezo/commit/3695e4335461942b00210c6270b4a1b7975e977a)

- Started Creality X-axis extruder breakout board [view commit](http://github.com/pyr0ball/pyr0piezo/commit/314d8407634d44479c0186c5eae5ecfb28dfce6c)

- Added pin assignments for serial/i2c comms on FFC [view commit](http://github.com/pyr0ball/pyr0piezo/commit/ced1d06a2517fc102c0fbaff3b9efa9f83a656d3)

- removed unused firmware, renamed existing to follow nomenclature [view commit](http://github.com/pyr0ball/pyr0piezo/commit/200702d12d9db8ec39f50706f1af2d618724c08c)

- Added component layout docs for rev.2.0.0 [view commit](http://github.com/pyr0ball/pyr0piezo/commit/1fa56d4d4170dcdb2e6393f03a2a21f0d5e40bd3)

- Added schematic for wiring up UART for programming [view commit](http://github.com/pyr0ball/pyr0piezo/commit/893bf50b727d5a25fc17d6ad6c78b0668cdbaf97)

- Finished trace routing for amp diagnostics pads [view commit](http://github.com/pyr0ball/pyr0piezo/commit/f1543700892755a30d23367644857b1afd3519e3)

### v2.0.0 to v2.0.1

Changelog updated 2019-08-15_15-50-29

  *Added Features*

------------------------------------

  *Bugfixes*

------------------------------------

  *Full Changelog*

- added ignore for openoffice text temp files [view commit](http://github.com/pyr0ball/pyr0piezo/commit/0117cc101ae249b4eb1af7ebf7b185271611753a)

- Added Pyr0-Piezo firmware update docs [view commit](http://github.com/pyr0ball/pyr0piezo/commit/e873d41e90dbff632e86e4fc01a1efcaf1af56cc)

- renamed firmware update docs [view commit](http://github.com/pyr0ball/pyr0piezo/commit/8598ce52728413d265515f294a9cf0971fc811c0)

- Finished first iteration of x-gantry board [view commit](http://github.com/pyr0ball/pyr0piezo/commit/b1e8562b8d2b72348bb47ebffa24bcd487700583)

- Added pdf of rev.2.0.0 schematic [view commit](http://github.com/pyr0ball/pyr0piezo/commit/3ff9d841c5286763927bbc8295a04bd02735e562)

- fixed some spacing and labelling [view commit](http://github.com/pyr0ball/pyr0piezo/commit/b7779f0994ec5734a231d787ef1c4329024402af)

- renamed latest v2.0.0 pdf [view commit](http://github.com/pyr0ball/pyr0piezo/commit/453bae33f532fe70d68559b7a308925f7e1ad546)

- aligned caps for easier soldering [view commit](http://github.com/pyr0ball/pyr0piezo/commit/afa62eca260721b62cc7890d2a49d9c357de42fc)

- Fixed PWM output syntax [view commit](http://github.com/pyr0ball/pyr0piezo/commit/2297f152071bde9b9c72eb6032e626e3b168ec5c)

- Renamed Rev.1.x.x sketch to match folder [view commit](http://github.com/pyr0ball/pyr0piezo/commit/e8300c9eb44d511c7ad4a008bfa52a4f24c707f6)

- Updated library and components [view commit](http://github.com/pyr0ball/pyr0piezo/commit/8084e65eeb616673e256f9daee7b14ec90465bc8)

### v2.0.1 to v2.0.1_hw

Changelog updated 2019-08-15_15-50-42

  *Added Features*

------------------------------------

  *Bugfixes*

------------------------------------

  *Full Changelog*

- Switched to 32VQFN package Atmega328pa [view commit](http://github.com/pyr0ball/pyr0piezo/commit/569439f82cc57f3d58e88b79d06484f87d9e5873)

- Swapped Atmega for ATSAMD21E family MCU [view commit](http://github.com/pyr0ball/pyr0piezo/commit/1ad0281ee2c193f10fb43cfa9358f9c613a2d923)

- added folder for wiki files, uploaded logo [view commit](http://github.com/pyr0ball/pyr0piezo/commit/2f3a3c1fd8aa2fc3d81cae42b5f66db14f4b51b9)

- repositioned filter cap for easier soldering [view commit](http://github.com/pyr0ball/pyr0piezo/commit/fbb90211c5628be56db9939539329b89c4244d84)

- Standardized naming conventions, organized [view commit](http://github.com/pyr0ball/pyr0piezo/commit/b3b5290996627fb8cc08e13e2c6c92da2d627a49)

- Swapped pins for 2-pin headers to match standard [view commit](http://github.com/pyr0ball/pyr0piezo/commit/26e9a0d09ce56b9ff0241210863d34c373ce454e)

- Replaced serial parser, verified parameters update [view commit](http://github.com/pyr0ball/pyr0piezo/commit/1a06027bc14d6377319968fa4168366cdb69f677)

- Added rudimentary i2c listener, fixed loop [view commit](http://github.com/pyr0ball/pyr0piezo/commit/55c6f867c20f665d069595652a5c63bec4fcfa90)

- fixed syntax preventing compilation [view commit](http://github.com/pyr0ball/pyr0piezo/commit/bd64d8f707d6094ca33924bc9ca01397c0e4fca1)

- Added wiring diagrams, fixed docs [view commit](http://github.com/pyr0ball/pyr0piezo/commit/729a44714dd2170215ec07227ea94218afc2438e)

- Added wiring diagram for DuetWifi [view commit](http://github.com/pyr0ball/pyr0piezo/commit/9bfc67574810060cf9c9c329ad0f97b5cc4f5a86)

- Added hookup guides for common MKS boards [view commit](http://github.com/pyr0ball/pyr0piezo/commit/f29ca9e5aa7d0152c57d00718987e8d45187d5c2)

- Updated description. Sync files [view commit](http://github.com/pyr0ball/pyr0piezo/commit/27302c9601c8e306e7446aa974edb9a7f371af4f)

- Begin sync of Rev.2.0.1 changes [view commit](http://github.com/pyr0ball/pyr0piezo/commit/4bfca9cf20c170b12c4c9a07bcffe8451b93c1fa)

- rotated fuse for easier soldering [view commit](http://github.com/pyr0ball/pyr0piezo/commit/c4eb8a81de483fd20dc31e9b590f8abd4c447066)

- sync all boards for Rev.2.0.1 before gerberization [view commit](http://github.com/pyr0ball/pyr0piezo/commit/5251e0f14a350c7e679900ce56b7a9115ec867e3)

### v2.0.1_hw to v2.0.2

Changelog updated 2019-08-15_15-50-56

  *Added Features*

------------------------------------

  *Bugfixes*

------------------------------------

  *Full Changelog*

- fixed syntax preventing compilation [view commit](http://github.com/pyr0ball/pyr0piezo/commit/bd64d8f707d6094ca33924bc9ca01397c0e4fca1)

- Added wiring diagrams, fixed docs [view commit](http://github.com/pyr0ball/pyr0piezo/commit/729a44714dd2170215ec07227ea94218afc2438e)

- Added wiring diagram for DuetWifi [view commit](http://github.com/pyr0ball/pyr0piezo/commit/9bfc67574810060cf9c9c329ad0f97b5cc4f5a86)

- Added hookup guides for common MKS boards [view commit](http://github.com/pyr0ball/pyr0piezo/commit/f29ca9e5aa7d0152c57d00718987e8d45187d5c2)

- Updated description. Sync files [view commit](http://github.com/pyr0ball/pyr0piezo/commit/27302c9601c8e306e7446aa974edb9a7f371af4f)

- Begin sync of Rev.2.0.1 changes [view commit](http://github.com/pyr0ball/pyr0piezo/commit/4bfca9cf20c170b12c4c9a07bcffe8451b93c1fa)

- rotated fuse for easier soldering [view commit](http://github.com/pyr0ball/pyr0piezo/commit/c4eb8a81de483fd20dc31e9b590f8abd4c447066)

- sync all boards for Rev.2.0.1 before gerberization [view commit](http://github.com/pyr0ball/pyr0piezo/commit/5251e0f14a350c7e679900ce56b7a9115ec867e3)

### v2.0.2 to v2.1.1

Changelog updated 2019-08-15_15-51-05

  *Added Features*

------------------------------------

  *Bugfixes*

------------------------------------

  *Full Changelog*

- fixed syntax preventing compilation [view commit](http://github.com/pyr0ball/pyr0piezo/commit/bd64d8f707d6094ca33924bc9ca01397c0e4fca1)

- Added wiring diagrams, fixed docs [view commit](http://github.com/pyr0ball/pyr0piezo/commit/729a44714dd2170215ec07227ea94218afc2438e)

- Added wiring diagram for DuetWifi [view commit](http://github.com/pyr0ball/pyr0piezo/commit/9bfc67574810060cf9c9c329ad0f97b5cc4f5a86)

- Added hookup guides for common MKS boards [view commit](http://github.com/pyr0ball/pyr0piezo/commit/f29ca9e5aa7d0152c57d00718987e8d45187d5c2)

- Updated description. Sync files [view commit](http://github.com/pyr0ball/pyr0piezo/commit/27302c9601c8e306e7446aa974edb9a7f371af4f)

- Begin sync of Rev.2.0.1 changes [view commit](http://github.com/pyr0ball/pyr0piezo/commit/4bfca9cf20c170b12c4c9a07bcffe8451b93c1fa)

- rotated fuse for easier soldering [view commit](http://github.com/pyr0ball/pyr0piezo/commit/c4eb8a81de483fd20dc31e9b590f8abd4c447066)

- sync all boards for Rev.2.0.1 before gerberization [view commit](http://github.com/pyr0ball/pyr0piezo/commit/5251e0f14a350c7e679900ce56b7a9115ec867e3)

- updated discord link [view commit](http://github.com/pyr0ball/pyr0piezo/commit/8de157958dae9ea0fd7f53a1cac44b39ce25035e)

- Added ESD protection diodes to motor connections [view commit](http://github.com/pyr0ball/pyr0piezo/commit/5d0c19afd30fc5a234c492d45b8ea2a7f43afb02)

- Brought library additions to older rev boards [view commit](http://github.com/pyr0ball/pyr0piezo/commit/a537393eefe19b5fc4bc6a698327124f2a28482a)

- Renamed X-car breakout for direct feed. [view commit](http://github.com/pyr0ball/pyr0piezo/commit/26d89f31fc7fbfbda53644e5ff64979b37415c1b)

- Merge readme before push [view commit](http://github.com/pyr0ball/pyr0piezo/commit/7c77e72e3f2ebdb2832fa2f3d5a589f16904899c)

- Beta production board sync [view commit](http://github.com/pyr0ball/pyr0piezo/commit/ad25ff868a5de61407c7ec868101ee26964bdfbb)

- Replaced license with CC-BY-SA-4.0 [view commit](http://github.com/pyr0ball/pyr0piezo/commit/9d082438c80de9a17d9650c0db352b9028f6f095)

- Updated eagle files for 1.0.2 for Eagle 9.0.2 [view commit](http://github.com/pyr0ball/pyr0piezo/commit/94645f8624ba07803f11df8cd59fb332a37fdd90)

- Updated link to license [view commit](http://github.com/pyr0ball/pyr0piezo/commit/4212ceeceb7f3cc5c90ed389c197ee09cdffd1f3)

- Adjusted capacitor placement for easier soldering [view commit](http://github.com/pyr0ball/pyr0piezo/commit/856ecafad23b30ac93f0411411ba67049d3f2bb7)

- fixed unary operators for adjustment logic [view commit](http://github.com/pyr0ball/pyr0piezo/commit/95ea64a822c5ebe54382ffc09dad919e67376aca)

- migrated floats to #define values [view commit](http://github.com/pyr0ball/pyr0piezo/commit/5ff215c0daa37907f0d2d51520a0604e842b2f90)

- Converting to defines and else ifs [view commit](http://github.com/pyr0ball/pyr0piezo/commit/e16c35cd3237f93d486dff2b78a39ff219935e10)

- Fixing debug vars in case they ever want to be used again [view commit](http://github.com/pyr0ball/pyr0piezo/commit/0e318eab7cb4cb030aabf4262e9101c1c774ed5d)

- Fixes for oscillating PWM output [view commit](http://github.com/pyr0ball/pyr0piezo/commit/5a6d5ca7db862b62aa5f27fe18bd6403006b0ff0)

- Merge branch 'master' into MinorOptimizations [view commit](http://github.com/pyr0ball/pyr0piezo/commit/c82c3e9bf55b17062fd1df469a01d98254a66b98)

- Merge pull request #25 from foodbandlt/MinorOptimizations [view commit](http://github.com/pyr0ball/pyr0piezo/commit/bcdae2e9e4525d2a2c4b07d6b42f6f7500b48827)

- Added function to alert the user when calibrating [view commit](http://github.com/pyr0ball/pyr0piezo/commit/37f7d4d085cbf336d7e1cc0d234dae49ee3d2d82)

- Set I2C input to be toggled by def [view commit](http://github.com/pyr0ball/pyr0piezo/commit/4c35d522596bd31e5bae9242b2a7780b87428acd)

- for v2.x this fixes https://github.com/pyr0ball/pyr0piezo/issues/28 [view commit](http://github.com/pyr0ball/pyr0piezo/commit/b5883af90136506015ddca7ca41a018aef581524)

- Separated functions and definitions [view commit](http://github.com/pyr0ball/pyr0piezo/commit/6567b50ddb28a442ffb91b8246665ba934dafa0f)

- fixed names for new files [view commit](http://github.com/pyr0ball/pyr0piezo/commit/7f1985d0cdb55af6ea88e4c4401460b15b1d9fab)

- changed adc calculations to use Vin reference [view commit](http://github.com/pyr0ball/pyr0piezo/commit/4b2186aaf71ee96594eaf6f230e06adef8cc69ec)

- fixed some ordering causing definition issues [view commit](http://github.com/pyr0ball/pyr0piezo/commit/1d098f184b58a3e85e43869e83ca12cdbbb6497c)

### v2.1.1 to v2.1.2

Changelog updated 2019-08-15_15-51-13

  *Added Features*

------------------------------------

  *Bugfixes*

------------------------------------

  *Full Changelog*

- Fixed "Flappy DAC" bug in rev.2.x.x firmware [view commit](http://github.com/pyr0ball/pyr0piezo/commit/f745940904f9e4af4e9a75ff3ffe168a2518b4d0)

- removed last remaining float, cleaned up unused vars [view commit](http://github.com/pyr0ball/pyr0piezo/commit/20454e7ffb0d32fd7aa7578649490b57134568f8)

- Added mkdocs for readthedocs integration [view commit](http://github.com/pyr0ball/pyr0piezo/commit/1f20019d57d4d50bbf4fdb2178ce5ae8366252a9)

- started adding structure to the site [view commit](http://github.com/pyr0ball/pyr0piezo/commit/69c9405e0f08e68050af5c0bdfed56c38c9fa024)

- switched to faster digitalWrite function for interrupt function [view commit](http://github.com/pyr0ball/pyr0piezo/commit/c22324021098b40ae3d145de02d9a4b982483493)

- added document structure, site output to gitignore [view commit](http://github.com/pyr0ball/pyr0piezo/commit/ba9c2abbe22b21696bf0dec05f87c4f34199d853)

- Merge branch 'master' of https://github.com/pyr0ball/pyr0piezo [view commit](http://github.com/pyr0ball/pyr0piezo/commit/1004840020b7a49969dc034f55e4339851b3901c)

- Added a few FAQ's [view commit](http://github.com/pyr0ball/pyr0piezo/commit/2b5d7e51f444391a95d58efc6acdb3609051d53b)

- Switched to task scheduler library for faster interrupt processing [view commit](http://github.com/pyr0ball/pyr0piezo/commit/0b1dbeb2379575af45a0b81dbfe441237a20794a)

- Created variable for voltmeter constant, fixed whitespace a bit [view commit](http://github.com/pyr0ball/pyr0piezo/commit/dc9ef32e5bff067ebb0acf9d2b1bc0007a0c4c1e)

- Complete overhaul of i2c code, created library structure [view commit](http://github.com/pyr0ball/pyr0piezo/commit/513d03a4bf52fc21c1c2b42982a32a5b3af59602)

- Changed compiler structure for including I2C [view commit](http://github.com/pyr0ball/pyr0piezo/commit/787745627764e890d1cb808f12393e87191a9a5f)

- Added i2c input handler for long variable [view commit](http://github.com/pyr0ball/pyr0piezo/commit/95ea53438168b0b97a91c80f7608a490d7a51955)

- Migrated configs to separate header file, made adjustment to definition [view commit](http://github.com/pyr0ball/pyr0piezo/commit/56c06008d4f7463a284561b5d0a337b573caa5e8)

- Changed compiler behavior for i2c. I2C library is still broken [view commit](http://github.com/pyr0ball/pyr0piezo/commit/29fd45db239fc5beee5414f8e795ab0e6d14cb96)
### v2.1.2 to v2.1.3

Changelog updated 2019-09-25_14-59-04

 *Added Features*

- setting up syntax for changelogs on the docs site  [view commit](http://github.com/pyr0ball/pyr0piezo/commit/b3909173a6b2a5d6cf281d9b6a4bb987599b960d) 

- Added comprehensive changelog generated from script  [view commit](http://github.com/pyr0ball/pyr0piezo/commit/74d348ea0738d7b17b176e1a6bc22478356a9dc4) 

- Added debug output to trigger function  [view commit](http://github.com/pyr0ball/pyr0piezo/commit/952a1cdb5f59be1e5ed3c2891674b01113c42c53) 

- Added gain factor to serial debug output  [view commit](http://github.com/pyr0ball/pyr0piezo/commit/fd172492d7231fa85606eeea16a0e6b3804834b9) 

- new version EasyPiezi-v2.1.2 - adds extra test points  [view commit](http://github.com/pyr0ball/pyr0piezo/commit/c79ad7d4bd6542f21c0715cb4b44e2b669b5d266) 

- added usage output to serial by sending <HELP>  [view commit](http://github.com/pyr0ball/pyr0piezo/commit/4d8466d79ab1a585bd651a670ea296856efaffdb) 

------------------------------------

 *Bugfixes*

- fixed syntax for table of contents on changelog  [view commit](http://github.com/pyr0ball/pyr0piezo/commit/359c8c8eba193dcc738dbb4bd49dbabb26972748) 

- added additional separator between sections added by changelog script  [view commit](http://github.com/pyr0ball/pyr0piezo/commit/ae26c4792bdd6c71721d7d552f588de34bd4fb8c) 

- commented out main loop trigger reset  [view commit](http://github.com/pyr0ball/pyr0piezo/commit/afad0a1d883980d6ef4709d63f58d407af9f4484) 

- fixed definition parameter for I2C config  [view commit](http://github.com/pyr0ball/pyr0piezo/commit/b207482bc1ca76ba21ae846b7446e1fdff65ab32) 

- Slight adjustment to wire routing for better spacing  [view commit](http://github.com/pyr0ball/pyr0piezo/commit/4b5cc640be4b0230fba5ac6a6c0e6388f8372091) 

- fixed footprint for RGB LED (default polarity was backwards)  [view commit](http://github.com/pyr0ball/pyr0piezo/commit/52f39b6debebb7995a301e34918917907bde0778) 

- fixed incorrect resistor values on FFC Direct vreg  [view commit](http://github.com/pyr0ball/pyr0piezo/commit/01c530d7c6efe6135643c05cc69230a04d021c35) 

- fixed 0606 rgb led footprint  [view commit](http://github.com/pyr0ball/pyr0piezo/commit/bc052bccacb0cd8ddf6b6ef20190d60698f783d3) 

- Fixed serial input updating the wrong variable  [view commit](http://github.com/pyr0ball/pyr0piezo/commit/cdae15c99ad3cdacc3209cb60f7fafbb7c123b3c) 

------------------------------------

 *Full Changelog*

- Migrated from single 60pin FFC to combined 15+40p [view commit](http://github.com/pyr0ball/pyr0piezo/commit/9ab87b5e7af8316f14d91f0f32905a2cf9bfe065) 

- Pushing 2.0.2 revised board files before 2.1.1 [view commit](http://github.com/pyr0ball/pyr0piezo/commit/20078fbba5095d68d17d7f252242ccdf624138eb) 

- Moved to dual FFC cable (15p-1MM + 40p-0.5mm) [view commit](http://github.com/pyr0ball/pyr0piezo/commit/288184df5825215cbb5168ce213882acb00053d9) 

- renamed wiki folder to assets [view commit](http://github.com/pyr0ball/pyr0piezo/commit/c35d25bfaca7ef677f694362d72bcc9297457546) 

- Added installation instructions (barely) [view commit](http://github.com/pyr0ball/pyr0piezo/commit/e64b380a74445b9f6ca6972e276d2281b6686246) 

- Merge branch 'master' of https://github.com/pyr0ball/pyr0piezo [view commit](http://github.com/pyr0ball/pyr0piezo/commit/012c1f795737ca8284d5820f06e5b173a3524201) 

- Added issue template for requesting a new mount [view commit](http://github.com/pyr0ball/pyr0piezo/commit/64d6b7170e7f2bd14590863803e55e8d12c258f6) 

- Added issue template to docs [view commit](http://github.com/pyr0ball/pyr0piezo/commit/9836a09d9815bd6af5e9a6b63725888c3dd5d27a) 

- Adding install docs filestructure [view commit](http://github.com/pyr0ball/pyr0piezo/commit/5c8083002abf5a97ba01641280d50dc61e172f87) 

- added a few other kinematics to the install structure [view commit](http://github.com/pyr0ball/pyr0piezo/commit/ae22f79a6bf08a04917e4dbc04dd12512339747c) 

- added menu structure and placeholder for hictop i3 [view commit](http://github.com/pyr0ball/pyr0piezo/commit/b1d58174f6b044423dc5ea50736fd7d7f7e50d0c) 

- fixed menu structure for mkdocs [view commit](http://github.com/pyr0ball/pyr0piezo/commit/f4992fcd6497ac6babd728b552baf52eefd7e4a9) 

- fixed typo with link for hictop i3 [view commit](http://github.com/pyr0ball/pyr0piezo/commit/7afba4fd389867e309a4d6ce35f0dedc032ccf8d) 

- fixed issue with markdown nested bullets on install page [view commit](http://github.com/pyr0ball/pyr0piezo/commit/9db343012f5d8d58d2d6081664139d3afae88049) 

- added images for instructions for mp-delta-mini [view commit](http://github.com/pyr0ball/pyr0piezo/commit/421dc64c5309ae4d5b0f392823863c9250e7b149) 

- added another pic for mp-delta-mini [view commit](http://github.com/pyr0ball/pyr0piezo/commit/f99fb90b26dbeabde37ded8b6cfadaa312624055) 

- renamed ultimaker to "quadrap" to better reflect nomenclature [view commit](http://github.com/pyr0ball/pyr0piezo/commit/da1355f67e769ca19fc217469b383b3114c3f75d) 

- renamed ultimaker to quadrap in main menu [view commit](http://github.com/pyr0ball/pyr0piezo/commit/38e144a0a2acef42ac2875345a4d01c0f4853e44) 

- Started on documentation for the Monoprice Delta Mini [view commit](http://github.com/pyr0ball/pyr0piezo/commit/d090a3ac410088fc06946538ec17d1a2b5d85caf) 

- fixed links in installation.md [view commit](http://github.com/pyr0ball/pyr0piezo/commit/a35d7144ba730c3adaa7acc5cbf3918f194aea1f) 

- fixed referential links in mp-delta-mini [view commit](http://github.com/pyr0ball/pyr0piezo/commit/25fcf6a4f852974dc23881da6e9f4a423b3c738a) 

- Added instructions for monoprice-delta-mini [view commit](http://github.com/pyr0ball/pyr0piezo/commit/9adfd8df13f709ec940abd4a55756fd96271a749) 

- added a link to MPDM's unofficial wiki [view commit](http://github.com/pyr0ball/pyr0piezo/commit/6d3e4e7c5ec851a7644a41253d954307ffb685e0) 

- renamed folders [view commit](http://github.com/pyr0ball/pyr0piezo/commit/a0cb30c778c3ced5e4866b2e2f98d68da63a45c2) 

- switched to material design theme for documentation site [view commit](http://github.com/pyr0ball/pyr0piezo/commit/cb10ee59afc1e9c3f57703d112152e2979da66a7) 

- Added Printer firmware configuration for Marlin [view commit](http://github.com/pyr0ball/pyr0piezo/commit/af1d2a9644de6f9e80da6d760fe82fabb4f67bfa) 

- fixed links and header formatting [view commit](http://github.com/pyr0ball/pyr0piezo/commit/670528cf853c4a4b99669d5b83a8eccce8cce52b) 

- added script for generating changelog from commits [view commit](http://github.com/pyr0ball/pyr0piezo/commit/13e468ea065c8aa26607f415b52e7863a8c65edc) 

- added favicon [view commit](http://github.com/pyr0ball/pyr0piezo/commit/4599c586ec86ea3625da7c6f9529bb54c0d592e7) 

- fixed typo in menu [view commit](http://github.com/pyr0ball/pyr0piezo/commit/02cd4381babbccbe45ddf04f0fa8b526161e2fe0) 

- added png favicon [view commit](http://github.com/pyr0ball/pyr0piezo/commit/eb376eaa08c4e16bf25582d310a706f825cd358e) 

- added info to the changelog script [view commit](http://github.com/pyr0ball/pyr0piezo/commit/7eb7fef94f2443a8c880bf94371dfed151dce220) 

- added extra functions to changelog script, added mkdocs deploy [view commit](http://github.com/pyr0ball/pyr0piezo/commit/83d4ba06536c27bbd056d8c018a7c9d176441fe8) 

- updated readme and about [view commit](http://github.com/pyr0ball/pyr0piezo/commit/89a2fcd202d6a3d09e5b3f3efcdb0e4277980d7e) 

- attempting to override site logo [view commit](http://github.com/pyr0ball/pyr0piezo/commit/af209b216f268ff2a2560cc0c83615f4d5807f97) 

- fixed override syntax [view commit](http://github.com/pyr0ball/pyr0piezo/commit/fcbbe91e9c0b4f053bff025b95a5ea379b856357) 

- new try [view commit](http://github.com/pyr0ball/pyr0piezo/commit/8d91bb4ce249e6b522ca2dab89224a89c8c28337) 

- fixing logo [view commit](http://github.com/pyr0ball/pyr0piezo/commit/6b25d6034b9a211f617fb3ca04b5d10b1438b66b) 

- Fixing favicon and site logo [view commit](http://github.com/pyr0ball/pyr0piezo/commit/fe7d7fc12e145c693f1e7f92b36e9d4471720abf) 

- fixing nested list spacing [view commit](http://github.com/pyr0ball/pyr0piezo/commit/dcb133f6c080a38ddcfdcb6e8d522375c1312d98) 

- resize header logo [view commit](http://github.com/pyr0ball/pyr0piezo/commit/3fae545d165c265db91a17785c78e571fa622377) 

- Added wiring diagram for Creality boards [view commit](http://github.com/pyr0ball/pyr0piezo/commit/834f0edd9840f88fec5847efae02224923f27fe1) 

- removed unneeded link [view commit](http://github.com/pyr0ball/pyr0piezo/commit/534d0a3af5f27c3e08b1df40a836ddb4ff2c5724) 

- added wiring diagrams [view commit](http://github.com/pyr0ball/pyr0piezo/commit/3d6435469051d23d1e9ce79310dd2bff6cf4fbd5) 

- Set theme jekyll-theme-hacker [view commit](http://github.com/pyr0ball/pyr0piezo/commit/50ac17b1408907bda199a0e1f5c8a98e752eb89b) 

- Update issue templates [view commit](http://github.com/pyr0ball/pyr0piezo/commit/a624b70024417635903ce4538bdb5e920ea7f674) 

- added links to schematics in main menu [view commit](http://github.com/pyr0ball/pyr0piezo/commit/978cdfc09f7712a68177fd664d16fd7e05201d6a) 

- added links for drawings [view commit](http://github.com/pyr0ball/pyr0piezo/commit/28cbdf5a7dfaf887b7a985a6ccea97bc273489ea) 

- rearranged files, added test pads layout [view commit](http://github.com/pyr0ball/pyr0piezo/commit/7a3f182198a4ad50f44baea8bd10e25af56ef0ac) 

- renamed drawing and schematics folders [view commit](http://github.com/pyr0ball/pyr0piezo/commit/6fb49d0695d9d32c5f06c8242c86d1f280c98196) 

- fixed typo in link [view commit](http://github.com/pyr0ball/pyr0piezo/commit/eb43d782b58c8ac4078c25a1640764e6904afdec) 

- fixed issue with pdf location [view commit](http://github.com/pyr0ball/pyr0piezo/commit/826d80b1ef3d8d7047234a1df63154f89ee009fb) 

- fixed embedded pdf layout size [view commit](http://github.com/pyr0ball/pyr0piezo/commit/52978f2190ab88eccbe8357a4c2199311c66be55) 

- added embedded content for easypiezi pinouts [view commit](http://github.com/pyr0ball/pyr0piezo/commit/93796ef50129b0f0f8f26050e093bbab7f47387c) 

- fixed syntax [view commit](http://github.com/pyr0ball/pyr0piezo/commit/ecfe4ce9f3eeb5943960b54a486ae310ea5826ae) 

- migrating more pages to embedded pdf [view commit](http://github.com/pyr0ball/pyr0piezo/commit/44b347371f1c1bac9be8303222e94930e1340748) 

- added embedded content to layouts section [view commit](http://github.com/pyr0ball/pyr0piezo/commit/568286fb4602497f0b40f83d3dc14593da3e61e0) 

- moved wiring diagrams section to installation [view commit](http://github.com/pyr0ball/pyr0piezo/commit/6c10e0eae5167eb2669e157dff772e54728b4899) 

- fixed some file encoding issues [view commit](http://github.com/pyr0ball/pyr0piezo/commit/70ca4a6f7f077320650b5938f72d37aaaca95567) 

- Fixed syntax issue with changelog script [view commit](http://github.com/pyr0ball/pyr0piezo/commit/11b8eb691f9091e57e7b5c387e041d60c8c8005b) 

- setting up syntax for changelogs on the docs site  [view commit](http://github.com/pyr0ball/pyr0piezo/commit/b3909173a6b2a5d6cf281d9b6a4bb987599b960d) 

- fixed some syntax with regex for the changelog [view commit](http://github.com/pyr0ball/pyr0piezo/commit/e4de789d65ae66166892cfd899ddd3761174e3c9) 

- Added comprehensive changelog generated from script  [view commit](http://github.com/pyr0ball/pyr0piezo/commit/74d348ea0738d7b17b176e1a6bc22478356a9dc4) 

- fixed syntax for table of contents on changelog  [view commit](http://github.com/pyr0ball/pyr0piezo/commit/359c8c8eba193dcc738dbb4bd49dbabb26972748) 

- added additional separator between sections added by changelog script  [view commit](http://github.com/pyr0ball/pyr0piezo/commit/ae26c4792bdd6c71721d7d552f588de34bd4fb8c) 

- Added latest commits to changelog including docs site [view commit](http://github.com/pyr0ball/pyr0piezo/commit/cc0b19d3913de537ce5d10201302643757b79f09) 

- commented out main loop trigger reset  [view commit](http://github.com/pyr0ball/pyr0piezo/commit/afad0a1d883980d6ef4709d63f58d407af9f4484) 

- fixed definition parameter for I2C config  [view commit](http://github.com/pyr0ball/pyr0piezo/commit/b207482bc1ca76ba21ae846b7446e1fdff65ab32) 

- Added debug output to trigger function  [view commit](http://github.com/pyr0ball/pyr0piezo/commit/952a1cdb5f59be1e5ed3c2891674b01113c42c53) 

- Added gain factor to serial debug output  [view commit](http://github.com/pyr0ball/pyr0piezo/commit/fd172492d7231fa85606eeea16a0e6b3804834b9) 

- removed tags from changelog public output [view commit](http://github.com/pyr0ball/pyr0piezo/commit/58bdb6035f41b391f0bede1c8b9190ed0e275bca) 

- added regex filter to changelog.sh [view commit](http://github.com/pyr0ball/pyr0piezo/commit/ceab2568950cfb56454c11ecf20e3f8cbecdafb2) 

- Slight adjustment to wire routing for better spacing  [view commit](http://github.com/pyr0ball/pyr0piezo/commit/4b5cc640be4b0230fba5ac6a6c0e6388f8372091) 

- fixed footprint for RGB LED (default polarity was backwards)  [view commit](http://github.com/pyr0ball/pyr0piezo/commit/52f39b6debebb7995a301e34918917907bde0778) 

- fixed incorrect resistor values on FFC Direct vreg  [view commit](http://github.com/pyr0ball/pyr0piezo/commit/01c530d7c6efe6135643c05cc69230a04d021c35) 

- fixed 0606 rgb led footprint  [view commit](http://github.com/pyr0ball/pyr0piezo/commit/bc052bccacb0cd8ddf6b6ef20190d60698f783d3) 

- new version EasyPiezi-v2.1.2 - adds extra test points  [view commit](http://github.com/pyr0ball/pyr0piezo/commit/c79ad7d4bd6542f21c0715cb4b44e2b669b5d266) 

- added usage output to serial by sending <HELP>  [view commit](http://github.com/pyr0ball/pyr0piezo/commit/4d8466d79ab1a585bd651a670ea296856efaffdb) 

- fixed permissions on scripts [view commit](http://github.com/pyr0ball/pyr0piezo/commit/914e0406336813f0b3c65c0462e3dc8f13288e82) 

- added new changelog detailing recent changes [view commit](http://github.com/pyr0ball/pyr0piezo/commit/c5a357d29036258f3221d9b38c50804e1578a04e) 

- Merge branch 'master' of https://github.com/pyr0ball/pyr0piezo [view commit](http://github.com/pyr0ball/pyr0piezo/commit/b8e008014d91845068ed843d04009ec2de150bae) 

- Fixed serial input updating the wrong variable  [view commit](http://github.com/pyr0ball/pyr0piezo/commit/cdae15c99ad3cdacc3209cb60f7fafbb7c123b3c) 

- added explaination on how to fine-tune VccMeter. #changelog [view commit](http://github.com/pyr0ball/pyr0piezo/commit/2bbc20ff4db69ab9eeacec7e10a45ebb6abbf3bf) 

- Merge branch 'master' of https://github.com/pyr0ball/pyr0piezo [view commit](http://github.com/pyr0ball/pyr0piezo/commit/a0d6b1d178052a160834aff3101a25c9e14a703d) 

- fixed typo #changelog [view commit](http://github.com/pyr0ball/pyr0piezo/commit/40b20c06701c4e4709961d153f5a9da8f45d9daf) 

------------------------------------
### v2.1.3 to v2.1.4

Changelog updated 2019-09-25_14-59-18

 *Added Features*

- Added EEPROM support for storing nvol settings  [view commit](http://github.com/pyr0ball/pyr0piezo/commit/5d72a5e817c182b90b1c9c7158d99bce744121f7) 

- complete overhaul of serial input and debug output  [view commit](http://github.com/pyr0ball/pyr0piezo/commit/9e885f316effc105f29027d1b859969f77477851) 

- updated serial input explaination to match new schema  [view commit](http://github.com/pyr0ball/pyr0piezo/commit/f4af33fe75c8306b567fdcaed92f238a0757499f) 

- Added input parameter for vref constant  [view commit](http://github.com/pyr0ball/pyr0piezo/commit/e416f1407251516217271dc6d09cad009e482987) 

------------------------------------

 *Bugfixes*

- synced nomenclature for vfollower variables  [view commit](http://github.com/pyr0ball/pyr0piezo/commit/9f172f1c1811d2084bfaf8771f36a87be4b083ab) 

- removed duplicate definition  [view commit](http://github.com/pyr0ball/pyr0piezo/commit/a58a7d029f7332c47529b393d8b9c7ec140cd19e) 

------------------------------------

 *Full Changelog*

- Initial PlatformIO conversion [view commit](http://github.com/pyr0ball/pyr0piezo/commit/b35e11696e97826a48bfd4b67bf968b803ecb49f) 

- Saving settings to EEPROM and other IMO sensible changes [view commit](http://github.com/pyr0ball/pyr0piezo/commit/6b9ea8ef06b5cac687a1fa3bb2bbc2e86cc9b85d) 

- Merge branch 'loredans-additions' of https://github.com/pyr0ball/pyr0piezo [view commit](http://github.com/pyr0ball/pyr0piezo/commit/14651c0d8a27d1431cde9436dea7f583e87e192f) 

- Updated gitignore, removed unnecessary files #changelog [view commit](http://github.com/pyr0ball/pyr0piezo/commit/4165075fa04e9d272c837c94496393b7f12da8a5) 

- Merge pull request #34 from loredan/master [view commit](http://github.com/pyr0ball/pyr0piezo/commit/6d471fd928e0e8528847f633a7832416d6675690) 

- synced nomenclature for vfollower variables  [view commit](http://github.com/pyr0ball/pyr0piezo/commit/9f172f1c1811d2084bfaf8771f36a87be4b083ab) 

- Added EEPROM support for storing nvol settings  [view commit](http://github.com/pyr0ball/pyr0piezo/commit/5d72a5e817c182b90b1c9c7158d99bce744121f7) 

- complete overhaul of serial input and debug output  [view commit](http://github.com/pyr0ball/pyr0piezo/commit/9e885f316effc105f29027d1b859969f77477851) 

- syntax cleanup #changelog [view commit](http://github.com/pyr0ball/pyr0piezo/commit/26d7a978d3b91ebc985dd5a2531db3ce93cce9ff) 

- more syntax fixes (from merge) #changelog [view commit](http://github.com/pyr0ball/pyr0piezo/commit/9ce36b86075be7ab63fc5a7872633c33d9f57950) 

- actually added some of the changes intended for previous commit [view commit](http://github.com/pyr0ball/pyr0piezo/commit/59387f85027443852feffed5704f2e4e79e9d95d) 

- restructured AVR firmware directory for vscode/PIO #changelog [view commit](http://github.com/pyr0ball/pyr0piezo/commit/6618f35f7d874082fde64678715ce25b670e8ce2) 

- migrated vscode comfig files [view commit](http://github.com/pyr0ball/pyr0piezo/commit/bf33ef43d7cdac37e594681d37dcbfd043756392) 

- updated serial input explaination to match new schema  [view commit](http://github.com/pyr0ball/pyr0piezo/commit/f4af33fe75c8306b567fdcaed92f238a0757499f) 

- Cleanup remaining merge files #changelog [view commit](http://github.com/pyr0ball/pyr0piezo/commit/5dd279775a475c2e9f271fbf0d9c5aacc25821de) 

- fixed variable typo [view commit](http://github.com/pyr0ball/pyr0piezo/commit/d00b0d078a732321b527347aaf95e33d84dfe3f0) 

- removed duplicate definition  [view commit](http://github.com/pyr0ball/pyr0piezo/commit/a58a7d029f7332c47529b393d8b9c7ec140cd19e) 

- Added input parameter for vref constant  [view commit](http://github.com/pyr0ball/pyr0piezo/commit/e416f1407251516217271dc6d09cad009e482987) 

- slight change in comment structure [view commit](http://github.com/pyr0ball/pyr0piezo/commit/aa6e3148a2f259023d83884bbcfd2365e75ee605) 

------------------------------------
### v2.1.3 to v2.1.4

Changelog updated 2019-10-09_20-40-12

 *Added Features*

- Added EEPROM support for storing nvol settings  [view commit](http://github.com/pyr0ball/pyr0piezo/commit/5d72a5e817c182b90b1c9c7158d99bce744121f7) 

- complete overhaul of serial input and debug output  [view commit](http://github.com/pyr0ball/pyr0piezo/commit/9e885f316effc105f29027d1b859969f77477851) 

- updated serial input explaination to match new schema  [view commit](http://github.com/pyr0ball/pyr0piezo/commit/f4af33fe75c8306b567fdcaed92f238a0757499f) 

- Added input parameter for vref constant  [view commit](http://github.com/pyr0ball/pyr0piezo/commit/e416f1407251516217271dc6d09cad009e482987) 

- Exported compiled firmware for m88p - v2.1.4  [view commit](http://github.com/pyr0ball/pyr0piezo/commit/4ff41f18ce0b1c58139e250de8a947de8211cd8f) 

- Added new test points to programmer jig  [view commit](http://github.com/pyr0ball/pyr0piezo/commit/4608808df5d13756ee0563760b4966b42072caaa) 

- Added script for updating through avrdude  [view commit](http://github.com/pyr0ball/pyr0piezo/commit/59649de11401ac68c487e2539305b01cd5bcd9b9) 

------------------------------------

 *Bugfixes*

- synced nomenclature for vfollower variables  [view commit](http://github.com/pyr0ball/pyr0piezo/commit/9f172f1c1811d2084bfaf8771f36a87be4b083ab) 

- removed duplicate definition  [view commit](http://github.com/pyr0ball/pyr0piezo/commit/a58a7d029f7332c47529b393d8b9c7ec140cd19e) 

- fixed variable type for vm-constant serial input  [view commit](http://github.com/pyr0ball/pyr0piezo/commit/9f1d5dfb6c923cb349de127ae237627c905ad175) 

- Fix for serial terminal line break symbol  [view commit](http://github.com/pyr0ball/pyr0piezo/commit/1d805b1ced3d1c07a6105e6280dc2316f6425020) 

- Reverted voltmeter code  [view commit](http://github.com/pyr0ball/pyr0piezo/commit/e029364cdcea0ae07c5702dc48b4dc2b74cbba6d) 

- Fixed serial command for voltmeter constant, added EEPROM support for it  [view commit](http://github.com/pyr0ball/pyr0piezo/commit/8d5fb81219f9ea9ae8dca7b5eee8c9b6f7a8ae1d) 

- Complete overhaul of FFC board for v2.1.2  [view commit](http://github.com/pyr0ball/pyr0piezo/commit/8b598199a0122cff55cdbacefbc72c38841108e6) 

------------------------------------

 *Full Changelog*

- Initial PlatformIO conversion [view commit](http://github.com/pyr0ball/pyr0piezo/commit/b35e11696e97826a48bfd4b67bf968b803ecb49f) 

- Saving settings to EEPROM and other IMO sensible changes [view commit](http://github.com/pyr0ball/pyr0piezo/commit/6b9ea8ef06b5cac687a1fa3bb2bbc2e86cc9b85d) 

- updated changelog to latest tag [view commit](http://github.com/pyr0ball/pyr0piezo/commit/5d24008dab89edf7b41f16f9e83349c5e0daf8bb) 

- Added section to readme about contributing [view commit](http://github.com/pyr0ball/pyr0piezo/commit/21a37ee2fd6b6ffb0c664d21897ed7691ac712ef) 

- Merge branch 'loredans-additions' of https://github.com/pyr0ball/pyr0piezo [view commit](http://github.com/pyr0ball/pyr0piezo/commit/14651c0d8a27d1431cde9436dea7f583e87e192f) 

- Updated gitignore, removed unnecessary files #changelog [view commit](http://github.com/pyr0ball/pyr0piezo/commit/4165075fa04e9d272c837c94496393b7f12da8a5) 

- Merge pull request #34 from loredan/master [view commit](http://github.com/pyr0ball/pyr0piezo/commit/6d471fd928e0e8528847f633a7832416d6675690) 

- synced nomenclature for vfollower variables  [view commit](http://github.com/pyr0ball/pyr0piezo/commit/9f172f1c1811d2084bfaf8771f36a87be4b083ab) 

- Added EEPROM support for storing nvol settings  [view commit](http://github.com/pyr0ball/pyr0piezo/commit/5d72a5e817c182b90b1c9c7158d99bce744121f7) 

- complete overhaul of serial input and debug output  [view commit](http://github.com/pyr0ball/pyr0piezo/commit/9e885f316effc105f29027d1b859969f77477851) 

- syntax cleanup #changelog [view commit](http://github.com/pyr0ball/pyr0piezo/commit/26d7a978d3b91ebc985dd5a2531db3ce93cce9ff) 

- more syntax fixes (from merge) #changelog [view commit](http://github.com/pyr0ball/pyr0piezo/commit/9ce36b86075be7ab63fc5a7872633c33d9f57950) 

- actually added some of the changes intended for previous commit [view commit](http://github.com/pyr0ball/pyr0piezo/commit/59387f85027443852feffed5704f2e4e79e9d95d) 

- restructured AVR firmware directory for vscode/PIO #changelog [view commit](http://github.com/pyr0ball/pyr0piezo/commit/6618f35f7d874082fde64678715ce25b670e8ce2) 

- migrated vscode comfig files [view commit](http://github.com/pyr0ball/pyr0piezo/commit/bf33ef43d7cdac37e594681d37dcbfd043756392) 

- updated serial input explaination to match new schema  [view commit](http://github.com/pyr0ball/pyr0piezo/commit/f4af33fe75c8306b567fdcaed92f238a0757499f) 

- Cleanup remaining merge files #changelog [view commit](http://github.com/pyr0ball/pyr0piezo/commit/5dd279775a475c2e9f271fbf0d9c5aacc25821de) 

- fixed variable typo [view commit](http://github.com/pyr0ball/pyr0piezo/commit/d00b0d078a732321b527347aaf95e33d84dfe3f0) 

- removed duplicate definition  [view commit](http://github.com/pyr0ball/pyr0piezo/commit/a58a7d029f7332c47529b393d8b9c7ec140cd19e) 

- Added input parameter for vref constant  [view commit](http://github.com/pyr0ball/pyr0piezo/commit/e416f1407251516217271dc6d09cad009e482987) 

- slight change in comment structure [view commit](http://github.com/pyr0ball/pyr0piezo/commit/aa6e3148a2f259023d83884bbcfd2365e75ee605) 

- added changelog for v2.1.4 (Loredan's Additions) [view commit](http://github.com/pyr0ball/pyr0piezo/commit/04c0c9ddb9dfe61d093e12c9085c4edd19363b3b) 

- Updated documentation and changelog [view commit](http://github.com/pyr0ball/pyr0piezo/commit/f13276cfe617e2e8ba19474f97c5901d7a4240c9) 

- fixed changelog headers [view commit](http://github.com/pyr0ball/pyr0piezo/commit/cf34ffdaef7ccb11abbcf87239b5fcac93fc7f98) 

- Merge pull request #35 from pyr0ball/loredans-additions [view commit](http://github.com/pyr0ball/pyr0piezo/commit/5f963d4dda9bb04f5665e1257c79b71913196f62) 

- documentation site formatting fixes [view commit](http://github.com/pyr0ball/pyr0piezo/commit/13a490d48f8763da503eb8c058b7ea603caa8c5f) 

- fixed variable type for vm-constant serial input  [view commit](http://github.com/pyr0ball/pyr0piezo/commit/9f1d5dfb6c923cb349de127ae237627c905ad175) 

- updated doc site nav link names [view commit](http://github.com/pyr0ball/pyr0piezo/commit/70ad44c5446d4fe61af9d8c70b26d94245b5cbf6) 

- Fix for serial terminal line break symbol  [view commit](http://github.com/pyr0ball/pyr0piezo/commit/1d805b1ced3d1c07a6105e6280dc2316f6425020) 

- fixed syntax error in includes section [view commit](http://github.com/pyr0ball/pyr0piezo/commit/55e2042925abcbba6cb1a279671312ff1996a76a) 

- Exported compiled firmware for m88p - v2.1.4  [view commit](http://github.com/pyr0ball/pyr0piezo/commit/4ff41f18ce0b1c58139e250de8a947de8211cd8f) 

- added compiled firmware for m328pb - v2.1.4 [view commit](http://github.com/pyr0ball/pyr0piezo/commit/056321a9e2d440502ba2b6bca57a022c24863f1e) 

- Merge branch 'master' of https://github.com/pyr0ball/pyr0piezo [view commit](http://github.com/pyr0ball/pyr0piezo/commit/a24e2ba97029aa76417927d5d576324ebe6c8342) 

- Reverted voltmeter code  [view commit](http://github.com/pyr0ball/pyr0piezo/commit/e029364cdcea0ae07c5702dc48b4dc2b74cbba6d) 

- Removed old debug output define and sensor trigger debug output, modified VComp and VFol output to mV instead of 10-bit number #changelog [view commit](http://github.com/pyr0ball/pyr0piezo/commit/6976b3908d76636679a2723dab972102adaba23f) 

- Fixed serial command for voltmeter constant, added EEPROM support for it  [view commit](http://github.com/pyr0ball/pyr0piezo/commit/8d5fb81219f9ea9ae8dca7b5eee8c9b6f7a8ae1d) 

- Fixed internal oscillator frequency configuration on ATmega88P, added configuration for ATmega328PB #changelog [view commit](http://github.com/pyr0ball/pyr0piezo/commit/51d734986b97ea8e070ab87eac70d871d057cfce) 

- Merge pull request #36 from loredan/master [view commit](http://github.com/pyr0ball/pyr0piezo/commit/d1171549a09bc0ec8592f636b75b06ef8888c07c) 

- Added new test points to programmer jig  [view commit](http://github.com/pyr0ball/pyr0piezo/commit/4608808df5d13756ee0563760b4966b42072caaa) 

- Added script for updating through avrdude  [view commit](http://github.com/pyr0ball/pyr0piezo/commit/59649de11401ac68c487e2539305b01cd5bcd9b9) 

- Merge branch 'loredans-additions' of https://github.com/pyr0ball/pyr0piezo into loredans-additions [view commit](http://github.com/pyr0ball/pyr0piezo/commit/03364f7509bd6ea5d5fc0e7f21d120f65bfd6587) 

- Code formatting unified [view commit](http://github.com/pyr0ball/pyr0piezo/commit/ecf28d89725a1c5c2d572805ca99c240a1882842) 

- code formatting [view commit](http://github.com/pyr0ball/pyr0piezo/commit/9126cd71a4b0a0570fe8f3b9295334bb94ac8ca3) 

- Merge pull request #37 from pyr0ball/loredans-additions [view commit](http://github.com/pyr0ball/pyr0piezo/commit/75d86cb8361cf4b6e9ba5d1f44d2a102a852eaba) 

- Complete overhaul of FFC board for v2.1.2  [view commit](http://github.com/pyr0ball/pyr0piezo/commit/8b598199a0122cff55cdbacefbc72c38841108e6) 

- Firmware shipped with Beta2 (v2.1.0) #changelog [view commit](http://github.com/pyr0ball/pyr0piezo/commit/e5e14583917c77ca48351c8057917f5a09ca2817) 

------------------------------------
### v2.1.4 to v2.1.5

Changelog updated 2019-10-30_18-51-54

 *Added Features*

- Added silkscreen of board revision for EzPz  [view commit](http://github.com/pyr0ball/pyr0piezo/commit/a91f8d6848e48c98fdf76a7ffa6ba939cb41c9b0) 

- added piezo-disk carrier boards by request  [view commit](http://github.com/pyr0ball/pyr0piezo/commit/0655da487ecc244ba4df18fe941a994796f60695) 

- Created DIY standalone board for use with external MCU  [view commit](http://github.com/pyr0ball/pyr0piezo/commit/98cc387b20a6d52af0343cddd30effe4b91d37e1) 

- new major version for addressing #48  [view commit](http://github.com/pyr0ball/pyr0piezo/commit/60e6f8d62b2bd8ed87a81bef3d61ac044e216713) 

- Exported Eagle parts library into project  [view commit](http://github.com/pyr0ball/pyr0piezo/commit/6fe3abe5f077498f81701c36427d5bb6ff173c46) 

- Added blank ino file for compatibility with arduino ide  [view commit](http://github.com/pyr0ball/pyr0piezo/commit/485797268932c58299642e06109ff2f74524d977) 

- Added serial feedback for trigger function  [view commit](http://github.com/pyr0ball/pyr0piezo/commit/5e69da1139207792025bde533b421896a33ebb5b) 

------------------------------------

 *Bugfixes*

- fixed polarity for trigger LED on DIY board  [view commit](http://github.com/pyr0ball/pyr0piezo/commit/5058ba29722eecd9b2440a12f4efd08edc60d91e) 

- Adds 1 to the blinkcount integer, trying to fix #49  [view commit](http://github.com/pyr0ball/pyr0piezo/commit/f8efc3d192da328ebaa0f9038c133dedaf4f9d0a) 

- fixed definition preventing serial response in #49  [view commit](http://github.com/pyr0ball/pyr0piezo/commit/266ae5cd9e0748a2fb6e4283090fa64711c4e8e7) 

- Fixed config reset #54  [view commit](http://github.com/pyr0ball/pyr0piezo/commit/8fea926ace694eebdb81a09cd86cd15ace10acbd) 

- final edit to fix #54  [view commit](http://github.com/pyr0ball/pyr0piezo/commit/81fb71a08ab3e1fd7af7358380386a68978a1136) 

------------------------------------

 *Documentation Updates*

- added documentation category to docs script  [view commit](http://github.com/pyr0ball/pyr0piezo/commit/322073f0d0be24ce182ad470ad84fb66b192bf04) 

- Added some images for v2.1.2 boards  [view commit](http://github.com/pyr0ball/pyr0piezo/commit/851cdbc2ba1fff399f671cb912952398802ef3b6) 

- added differentiation in docs structure between versions  [view commit](http://github.com/pyr0ball/pyr0piezo/commit/d09f40e70673aff838fadfc03b78731639458eba) 

- removed redundant changelog file  [view commit](http://github.com/pyr0ball/pyr0piezo/commit/215a6c3567cb58bb1afaf1f2a44073df8db39e90) 

- Updated piezo config docs with serial applications  [view commit](http://github.com/pyr0ball/pyr0piezo/commit/d77ba16ccae9fd1df0dcf5fe99d10f4218b499f5) 

- Added beginning of doc explaining circuit settings  [view commit](http://github.com/pyr0ball/pyr0piezo/commit/5fcdb578c912223b70448da2480370650e816dd7) 

- documentation formatting fixes  [view commit](http://github.com/pyr0ball/pyr0piezo/commit/83e39f5debf331f75021ebf3e2959892d1dd3e51) 

- typo fix in docs  [view commit](http://github.com/pyr0ball/pyr0piezo/commit/eeb2298bd6527a8691adcdde9871cd954ad13203) 

- renamed Eagle Files to reflect product name  [view commit](http://github.com/pyr0ball/pyr0piezo/commit/95d211825643e7a5e3d456082fe428fdec855ecd) 

- Added page for PT100 RTD sensor  [view commit](http://github.com/pyr0ball/pyr0piezo/commit/9445ce76cffe2bf4394f930a459baf1ddabe0ad7) 

- Added PT100 to docs site nav  [view commit](http://github.com/pyr0ball/pyr0piezo/commit/6bb10d4cc6ecc801ce412a8240888de18939387e) 

- attempting to fix the discord widget in README  [view commit](http://github.com/pyr0ball/pyr0piezo/commit/bf4b1a3ef00fa537d02c573a29e1e6335a3ab866) 

------------------------------------

 *Full Changelog*

- analogWrite is replaced with native phase correct PWM, 4kHz 10-bit on comparator and 16kHz 8-bit on voltage follower  [view commit](http://github.com/pyr0ball/pyr0piezo/commit/14032ba3252b1b75f42ded4cc6ed8a8c9dc94a59) 

- Merge pull request #38 from loredan/master [view commit](http://github.com/pyr0ball/pyr0piezo/commit/a23ce17bbe13af5b159aff063b8219df99b783ef) 

- updated documentation for i3 mounts [view commit](http://github.com/pyr0ball/pyr0piezo/commit/f1afd523973e408dd6d566c7162a6dd84ce05e84) 

- added documentation category to docs script  [view commit](http://github.com/pyr0ball/pyr0piezo/commit/322073f0d0be24ce182ad470ad84fb66b192bf04) 

- Merge branch 'master' of https://github.com/pyr0ball/pyr0piezo [view commit](http://github.com/pyr0ball/pyr0piezo/commit/bcdeec20c7318e35f363d39f8703310db44df3e1) 

- Added some images for v2.1.2 boards  [view commit](http://github.com/pyr0ball/pyr0piezo/commit/851cdbc2ba1fff399f671cb912952398802ef3b6) 

- added differentiation in docs structure between versions  [view commit](http://github.com/pyr0ball/pyr0piezo/commit/d09f40e70673aff838fadfc03b78731639458eba) 

- Merge branch 'master' of https://github.com/pyr0ball/pyr0piezo [view commit](http://github.com/pyr0ball/pyr0piezo/commit/607a20523256a70bfec6e0782c8d374e4fc6834c) 

- removed redundant changelog file  [view commit](http://github.com/pyr0ball/pyr0piezo/commit/215a6c3567cb58bb1afaf1f2a44073df8db39e90) 

- Added silkscreen of board revision for EzPz  [view commit](http://github.com/pyr0ball/pyr0piezo/commit/a91f8d6848e48c98fdf76a7ffa6ba939cb41c9b0) 

- Merge branch 'master' of https://github.com/pyr0ball/pyr0piezo [view commit](http://github.com/pyr0ball/pyr0piezo/commit/0dc3e5913e83fc537d5508505ca9ae5c48e44472) 

- Merge branch 'loredans-additions' of https://github.com/pyr0ball/pyr0piezo [view commit](http://github.com/pyr0ball/pyr0piezo/commit/b7b40be14bc98ca72fb9f895a1d7d05b4a55e05d) 

- Merge branch 'master' of https://github.com/pyr0ball/pyr0piezo [view commit](http://github.com/pyr0ball/pyr0piezo/commit/5cbd1ae13109c612b875c751688d4a4d3493e3de) 

- Updated piezo config docs with serial applications  [view commit](http://github.com/pyr0ball/pyr0piezo/commit/d77ba16ccae9fd1df0dcf5fe99d10f4218b499f5) 

- Added beginning of doc explaining circuit settings  [view commit](http://github.com/pyr0ball/pyr0piezo/commit/5fcdb578c912223b70448da2480370650e816dd7) 

- documentation formatting fixes  [view commit](http://github.com/pyr0ball/pyr0piezo/commit/83e39f5debf331f75021ebf3e2959892d1dd3e51) 

- typo fix in docs  [view commit](http://github.com/pyr0ball/pyr0piezo/commit/eeb2298bd6527a8691adcdde9871cd954ad13203) 

- added piezo-disk carrier boards by request  [view commit](http://github.com/pyr0ball/pyr0piezo/commit/0655da487ecc244ba4df18fe941a994796f60695) 

- pull before push [view commit](http://github.com/pyr0ball/pyr0piezo/commit/f38b559da85933daae14679d3e7a6b02086cadcd) 

- pull before push [view commit](http://github.com/pyr0ball/pyr0piezo/commit/b0225496a4cce878bb54ccbb0a713fd7f8ab78e3) 

- Created DIY standalone board for use with external MCU  [view commit](http://github.com/pyr0ball/pyr0piezo/commit/98cc387b20a6d52af0343cddd30effe4b91d37e1) 

- fixed polarity for trigger LED on DIY board  [view commit](http://github.com/pyr0ball/pyr0piezo/commit/5058ba29722eecd9b2440a12f4efd08edc60d91e) 

- Merge branch 'master' of https://github.com/pyr0ball/pyr0piezo [view commit](http://github.com/pyr0ball/pyr0piezo/commit/884d65690a451189327394686514dcd56b728eb8) 

- renamed Eagle Files to reflect product name  [view commit](http://github.com/pyr0ball/pyr0piezo/commit/95d211825643e7a5e3d456082fe428fdec855ecd) 

- Added page for PT100 RTD sensor  [view commit](http://github.com/pyr0ball/pyr0piezo/commit/9445ce76cffe2bf4394f930a459baf1ddabe0ad7) 

- Added PT100 to docs site nav  [view commit](http://github.com/pyr0ball/pyr0piezo/commit/6bb10d4cc6ecc801ce412a8240888de18939387e) 

- attempting to fix the discord widget in README  [view commit](http://github.com/pyr0ball/pyr0piezo/commit/bf4b1a3ef00fa537d02c573a29e1e6335a3ab866) 

- new major version for addressing #48  [view commit](http://github.com/pyr0ball/pyr0piezo/commit/60e6f8d62b2bd8ed87a81bef3d61ac044e216713) 

- Adds 1 to the blinkcount integer, trying to fix #49  [view commit](http://github.com/pyr0ball/pyr0piezo/commit/f8efc3d192da328ebaa0f9038c133dedaf4f9d0a) 

- fixed definition preventing serial response in #49  [view commit](http://github.com/pyr0ball/pyr0piezo/commit/266ae5cd9e0748a2fb6e4283090fa64711c4e8e7) 

- Fix clearing stored config on restore [view commit](http://github.com/pyr0ball/pyr0piezo/commit/62770a65d88a3d8197709fa4a2b2e1cc7ca96f90) 

- Merge pull request #51 from foodbandlt/bugfix [view commit](http://github.com/pyr0ball/pyr0piezo/commit/db1215db9393e0cf4d0633f1670ccbf964da04df) 

- Exported Eagle parts library into project  [view commit](http://github.com/pyr0ball/pyr0piezo/commit/6fe3abe5f077498f81701c36427d5bb6ff173c46) 

- Merge branch 'loredans-additions' of https://github.com/pyr0ball/pyr0piezo into loredans-additions [view commit](http://github.com/pyr0ball/pyr0piezo/commit/48fe419943d50ff236114488d5093e0ab0c4debe) 

- Merge pull request #53 from pyr0ball/loredans-additions [view commit](http://github.com/pyr0ball/pyr0piezo/commit/9e2862ca08cca46b1dad322688522deb658b7231) 

- Added blank ino file for compatibility with arduino ide  [view commit](http://github.com/pyr0ball/pyr0piezo/commit/485797268932c58299642e06109ff2f74524d977) 

- added avrdude.conf for terminal uploading [view commit](http://github.com/pyr0ball/pyr0piezo/commit/16ccd72a5dfe60e59260d5476282e1fc0899d7f5) 

- Fixed config reset #54  [view commit](http://github.com/pyr0ball/pyr0piezo/commit/8fea926ace694eebdb81a09cd86cd15ace10acbd) 

- Merge pull request #55 from loredan/master [view commit](http://github.com/pyr0ball/pyr0piezo/commit/a0cc8b4ac7737078552edbe789e26022931d8975) 

- Merge branch 'master' of https://github.com/pyr0ball/pyr0piezo [view commit](http://github.com/pyr0ball/pyr0piezo/commit/a09a5c8e4ed55cef0112e917648af3d6cc2fda86) 

- final edit to fix #54  [view commit](http://github.com/pyr0ball/pyr0piezo/commit/81fb71a08ab3e1fd7af7358380386a68978a1136) 

- Added serial feedback for trigger function  [view commit](http://github.com/pyr0ball/pyr0piezo/commit/5e69da1139207792025bde533b421896a33ebb5b) 

- Fix EEPROM saving issue when issuing a RESET command via a serial terminal. [view commit](http://github.com/pyr0ball/pyr0piezo/commit/22d4535e79e09416c48ec0bdbb3e18b1c3ea3430) 

- Update .gitignore [view commit](http://github.com/pyr0ball/pyr0piezo/commit/13d8b32b59bb481768c44eed08d2fb6476c72a4b) 

- Update .gitignore [view commit](http://github.com/pyr0ball/pyr0piezo/commit/7cdb535fdfc5b6280eab2265c2807bb9298b60f7) 

- This code change reduces the amount of EEPROM writes that could potentially occur within a short period of time, thus making the EEPROM last longer. [view commit](http://github.com/pyr0ball/pyr0piezo/commit/0e7862c3c48773e81af0f31992e36e410a1f1e11) 

- Merge pull request #57 from klcjr89/master [view commit](http://github.com/pyr0ball/pyr0piezo/commit/61d7bd659bdc3324dff53e47b6d58ed32182418c) 

- Finish implementing digitalWriteFast to save MCU cycles. [view commit](http://github.com/pyr0ball/pyr0piezo/commit/97296db236e83a17a12608afe66667b085a1376f) 

- Code change implements analogReadFast, which reduces the read time of an anolog pin from 112 µS down to 21 µS. [view commit](http://github.com/pyr0ball/pyr0piezo/commit/eb052133a3e8ff98adfc93e52984e0c1b626b0d0) 

- Merge pull request #58 from klcjr89/master [view commit](http://github.com/pyr0ball/pyr0piezo/commit/98c2f0ff8d076e0a49ced19b44f48bc967a30465) 

- Merge pull request #59, implement "fast" pin operations [view commit](http://github.com/pyr0ball/pyr0piezo/commit/bcc7b254848091533b7deb3d211f6bcc399fe6ba) 

------------------------------------
### v2.1.5 to v2.1.6

Changelog updated 2019-12-28_03-43-10

 *Added Features*

- Adds support for inverting trigger logic.   [view commit](http://github.com/pyr0ball/pyr0piezo/commit/5b8c409c109954ea520e5c1e6de9c1f0834889c2) 

------------------------------------

 *Bugfixes*

- Fixed width of thermals on singledisk adapter  [view commit](http://github.com/pyr0ball/pyr0piezo/commit/024c6f79111242985d1ce0a0b3ad4358f0d885bf) 

- Fixed pad thermals, added url, fixed logo  [view commit](http://github.com/pyr0ball/pyr0piezo/commit/041836b40b0e0d6fce617c9f73365e8ca9ecb076) 

- Fix for gain adjustment  [view commit](http://github.com/pyr0ball/pyr0piezo/commit/94e2c127951575f3847e72235969a1623eac13a4) 

- fixing serial input not taking effect immediately  [view commit](http://github.com/pyr0ball/pyr0piezo/commit/4076423e1babf8e6e45f1878481dfe42f29fe211) 

------------------------------------

 *Documentation Updates*

- Documentation update for v2.1.5  [view commit](http://github.com/pyr0ball/pyr0piezo/commit/5d72861a36e1e76c1264d3bc8b02479edc6d3979) 

------------------------------------

 *Full Changelog*

- Documentation update for v2.1.5  [view commit](http://github.com/pyr0ball/pyr0piezo/commit/5d72861a36e1e76c1264d3bc8b02479edc6d3979) 

- These code changes are for resetting the config values to the default values by issuing the ERASE word via a serial terminal. [view commit](http://github.com/pyr0ball/pyr0piezo/commit/106e6c85c3c5f97e20d947a8b6ea3a6f8f30a268) 

- Merge pull request #60 from klcjr89/master [view commit](http://github.com/pyr0ball/pyr0piezo/commit/9ae410f011c43e5bf4ccb902ef1734d0a61edb28) 

- Fixed width of thermals on singledisk adapter  [view commit](http://github.com/pyr0ball/pyr0piezo/commit/024c6f79111242985d1ce0a0b3ad4358f0d885bf) 

- Fixed pad thermals, added url, fixed logo  [view commit](http://github.com/pyr0ball/pyr0piezo/commit/041836b40b0e0d6fce617c9f73365e8ca9ecb076) 

- Merge branch 'master' of https://github.com/pyr0ball/pyr0piezo [view commit](http://github.com/pyr0ball/pyr0piezo/commit/cd3503beb31c346c0f0f1a1cc53c6ba1a06c57a3) 

- Merge branch 'master' of https://github.com/pyr0ball/pyr0piezo into develop [view commit](http://github.com/pyr0ball/pyr0piezo/commit/64550544467b6e2e5627938338ac63c5a39c5b9b) 

- removed file that shouldn't be tracked [view commit](http://github.com/pyr0ball/pyr0piezo/commit/4f3558b79198da40932a678d410cca57b1e0d801) 

- slight edit to platformio.ini, added dependencies [view commit](http://github.com/pyr0ball/pyr0piezo/commit/bc2de746b469d2f04452b55baafd523cc7e335da) 

- Merge branch 'master' of https://github.com/pyr0ball/pyr0piezo into develop [view commit](http://github.com/pyr0ball/pyr0piezo/commit/407c9834d1c8e9db58041ba84cbe5064d64e20d8) 

- Adds support for inverting trigger logic.   [view commit](http://github.com/pyr0ball/pyr0piezo/commit/5b8c409c109954ea520e5c1e6de9c1f0834889c2) 

- ignore [view commit](http://github.com/pyr0ball/pyr0piezo/commit/0d73cc55ef50b1bd11193d47e42e2f0afad97601) 

- Merge branch 'master' of https://github.com/pyr0ball/pyr0piezo [view commit](http://github.com/pyr0ball/pyr0piezo/commit/e0ebe53efcb320a8ba2d552461838486075b0d3b) 

- Fix for gain adjustment  [view commit](http://github.com/pyr0ball/pyr0piezo/commit/94e2c127951575f3847e72235969a1623eac13a4) 

- Merge branch 'develop' of https://github.com/pyr0ball/pyr0piezo into develop [view commit](http://github.com/pyr0ball/pyr0piezo/commit/75776942085c672776ceaa32988dce46d45389a2) 

- Merge pull request #63 from loredan/master [view commit](http://github.com/pyr0ball/pyr0piezo/commit/ecd472d80f0a7a46bc7a6d5eddbbe107c6ed22ed) 

- Merge branch 'develop' of https://github.com/pyr0ball/pyr0piezo into develop [view commit](http://github.com/pyr0ball/pyr0piezo/commit/d30c60639c6a0f82697a97257e89b2291526aa0e) 

- fixing serial input not taking effect immediately  [view commit](http://github.com/pyr0ball/pyr0piezo/commit/4076423e1babf8e6e45f1878481dfe42f29fe211) 

- fixed accidental reversal of gain adjust #oops [view commit](http://github.com/pyr0ball/pyr0piezo/commit/3dcadb5e4ee9449eafdcd9f9861ba8b142373eb1) 

- Revert "fixed accidental reversal of gain adjust #oops" [view commit](http://github.com/pyr0ball/pyr0piezo/commit/2e4cf0ce58e460622cf5e639a15f78481c319839) 

------------------------------------
### v2.2.0 to v2.2.1

Changelog updated 2020-01-16_11-24-38

 *Added Features*

- modified i2c registermap, added stubs  [view commit](http://github.com/pyr0ball/pyr0piezo/commit/44bd9f0182551668aaab3dc2de385f5a79deab13) 

- added firmware version to serial response  [view commit](http://github.com/pyr0ball/pyr0piezo/commit/a3e4ec86a50ed991f97b5f85aabd0a15fd036d81) 

- Changed default state of I2C input macro to enabled  [view commit](http://github.com/pyr0ball/pyr0piezo/commit/217c13b82700d58774b874f0865f5ca04f3cc418) 

- changed error LED behavor to instead indicate a trigger event  [view commit](http://github.com/pyr0ball/pyr0piezo/commit/a1267204d5403a3fcd20f680be75cc6753366ca9) 

------------------------------------

 *Bugfixes*

- fixed platformio.ini to allow build and upload directly  [view commit](http://github.com/pyr0ball/pyr0piezo/commit/79f0d657dae01ad02d266a6bccb526845505fa5f) 

- fixed logic and pzdet inputs  [view commit](http://github.com/pyr0ball/pyr0piezo/commit/c30905bd74cbeee65109ae18643ec04123abecbd) 

- fixed logic level change not taking effect til trigger  [view commit](http://github.com/pyr0ball/pyr0piezo/commit/a9d928833ae6d14214eb6c7c8d67bd5974ad9e74) 

- changed compiler to include help message only on 328pb  [view commit](http://github.com/pyr0ball/pyr0piezo/commit/49bfe7663be0cf019b0fa1aa846345dbcf57a6e5) 

- fixed missing semicolon  [view commit](http://github.com/pyr0ball/pyr0piezo/commit/568dc93311a8d3494a61e922cccb929b97420f75) 

------------------------------------

 *Documentation Updates*

- Updated changelog  [view commit](http://github.com/pyr0ball/pyr0piezo/commit/30999ed4a85cdaa3950d054585f2e8e1aa40b08a) 

- added instructions for PZDET and LOGIC to main.cpp  [view commit](http://github.com/pyr0ball/pyr0piezo/commit/e668988f3e19932119ac72bfea4e37bb68af4197) 

- added docs for wiring up UART and uploading firmware  [view commit](http://github.com/pyr0ball/pyr0piezo/commit/7d352360d959c2db4ea76a79ba3f1acb30223905) 

- fixed typo in link to uart pdf  [view commit](http://github.com/pyr0ball/pyr0piezo/commit/5e82dc5cd52ab07667528740195c2beb0991256a) 

- fixed another typo in docs  [view commit](http://github.com/pyr0ball/pyr0piezo/commit/85b63734d758edf3e3b1204091920ffe8ed0068f) 

- Added wiring image for ezpz uart  [view commit](http://github.com/pyr0ball/pyr0piezo/commit/882a8721f0f0c8cd4eefa72273038afe15239471) 

------------------------------------

 *Full Changelog*

- Updated changelog  [view commit](http://github.com/pyr0ball/pyr0piezo/commit/30999ed4a85cdaa3950d054585f2e8e1aa40b08a) 

- fixed platformio.ini to allow build and upload directly  [view commit](http://github.com/pyr0ball/pyr0piezo/commit/79f0d657dae01ad02d266a6bccb526845505fa5f) 

- removed bad merge lines [view commit](http://github.com/pyr0ball/pyr0piezo/commit/d903a8a4f371f1ab5a2dbd87b2ae19bf4c0ac080) 

- fixed logic and pzdet inputs  [view commit](http://github.com/pyr0ball/pyr0piezo/commit/c30905bd74cbeee65109ae18643ec04123abecbd) 

- added instructions for PZDET and LOGIC to main.cpp  [view commit](http://github.com/pyr0ball/pyr0piezo/commit/e668988f3e19932119ac72bfea4e37bb68af4197) 

- fixed logic level change not taking effect til trigger  [view commit](http://github.com/pyr0ball/pyr0piezo/commit/a9d928833ae6d14214eb6c7c8d67bd5974ad9e74) 

- changed compiler to include help message only on 328pb  [view commit](http://github.com/pyr0ball/pyr0piezo/commit/49bfe7663be0cf019b0fa1aa846345dbcf57a6e5) 

- fixed missing semicolon  [view commit](http://github.com/pyr0ball/pyr0piezo/commit/568dc93311a8d3494a61e922cccb929b97420f75) 

- added verbose output to PIO build flags [view commit](http://github.com/pyr0ball/pyr0piezo/commit/539e5d141125f04c009c2347d187fdfc84b5c451) 

- modified i2c registermap, added stubs  [view commit](http://github.com/pyr0ball/pyr0piezo/commit/44bd9f0182551668aaab3dc2de385f5a79deab13) 

- added docs for wiring up UART and uploading firmware  [view commit](http://github.com/pyr0ball/pyr0piezo/commit/7d352360d959c2db4ea76a79ba3f1acb30223905) 

- fixed typo in link to uart pdf  [view commit](http://github.com/pyr0ball/pyr0piezo/commit/5e82dc5cd52ab07667528740195c2beb0991256a) 

- fixed another typo in docs  [view commit](http://github.com/pyr0ball/pyr0piezo/commit/85b63734d758edf3e3b1204091920ffe8ed0068f) 

- Added wiring image for ezpz uart  [view commit](http://github.com/pyr0ball/pyr0piezo/commit/882a8721f0f0c8cd4eefa72273038afe15239471) 

- added firmware version to serial response  [view commit](http://github.com/pyr0ball/pyr0piezo/commit/a3e4ec86a50ed991f97b5f85aabd0a15fd036d81) 

- changed default state for i2c input macro to enabled  [view commit](http://github.com/pyr0ball/pyr0piezo/commit/904d6af9dc3e74aeae190cde418338f80e906e84) 

- Changed default state of I2C input macro to enabled  [view commit](http://github.com/pyr0ball/pyr0piezo/commit/217c13b82700d58774b874f0865f5ca04f3cc418) 

- changed error LED behavor to instead indicate a trigger event  [view commit](http://github.com/pyr0ball/pyr0piezo/commit/a1267204d5403a3fcd20f680be75cc6753366ca9) 

------------------------------------
### v2.2.1 to v2.3.0

Changelog updated 2020-05-10_15-07-19

 *Added Features*

- Autogenerating version number #featureadd [view commit](http://github.com/pyr0ball/pyr0piezo/commit/5cf9c4e94a3b14414befba0423b0cb3273846a4c)

- Added FFC-X-Mot board for v2.1.2  [view commit](http://github.com/pyr0ball/pyr0piezo/commit/9db036fc1ee13d3b5176fb5bf5b92bc0b1705af0) 

- Added eagle source files for SingleDisk PCB adapters  [view commit](http://github.com/pyr0ball/pyr0piezo/commit/6b6d13e08fdaa915b19635e5706014ff1557589d) 

- added configs for new features logic level and pzdet  [view commit](http://github.com/pyr0ball/pyr0piezo/commit/a4a9cb90813fc5e266a67536046f3ae7843fea3a) 

- updated eagle parts library to latest  [view commit](http://github.com/pyr0ball/pyr0piezo/commit/83e43f34ae264cc559ccf97175229d012f8606b7) 

- Added support for either 5v or 3.3v operation  [view commit](http://github.com/pyr0ball/pyr0piezo/commit/b1830500647f918d589c5a2789fab86cfa5f2167) 

- updated parts library with new logo and TH parts  [view commit](http://github.com/pyr0ball/pyr0piezo/commit/b4ea4d7b3e801fa4bebc78481b3216e79aae7109) 

- Built pyr0-piezo v2 circuit on a business card  [view commit](http://github.com/pyr0ball/pyr0piezo/commit/d41e24f2eadb59d8c6f5cf00d4713b647d4d98bf) 

- added compiled firmware used on MPDM  [view commit](http://github.com/pyr0ball/pyr0piezo/commit/8838301821af1c50062aa33850ca78bdb6a1e888) 

- Added code for switching between 3.3v and 5v signal output  [view commit](http://github.com/pyr0ball/pyr0piezo/commit/12f86c971b6423e21b550d0ae3377014a091d48b) 

- Serial commands are now case-insensitive  [view commit](http://github.com/pyr0ball/pyr0piezo/commit/2f4e42d34a00b0e58e4ca3b12aa95ce10a417e57) 

- Added user-friendty VCC readings adjustment  Minor fixes to i2c #bugfix [view commit](http://github.com/pyr0ball/pyr0piezo/commit/65dbe60c877d7df285dea69503dcf04b4e33f95f) 

------------------------------------

 *Bugfixes*

- updated v2.2.0 eagle files with latest library parts  [view commit](http://github.com/pyr0ball/pyr0piezo/commit/2e8d5cba4c94b07c971bc0f6fb4b212f942b47e4) 

- gave singledisk pcb a bit more flex for better sensitivity  [view commit](http://github.com/pyr0ball/pyr0piezo/commit/0de1676e642282700ff34fe56c29fd853e1f06e2) 

- updated piezoPCB singledisk for better actuation  [view commit](http://github.com/pyr0ball/pyr0piezo/commit/effa5c7d7faf5e5383f9e7b8dcab6c5f0658d752) 

- trying to eliminate those pesky lbr temp files again  [view commit](http://github.com/pyr0ball/pyr0piezo/commit/db0e457450fa9ba14a52c7b514dc4d7800f73a21) 

- Added user-friendty VCC readings adjustment #featureadd Minor fixes to i2c  [view commit](http://github.com/pyr0ball/pyr0piezo/commit/65dbe60c877d7df285dea69503dcf04b4e33f95f) 

- fixed string concatentate issue on version_git.py  [view commit](http://github.com/pyr0ball/pyr0piezo/commit/74eabff95006689712e1e82c747ca5aed931c24f) 

------------------------------------

 *Documentation Updates*

- updated internal version with latest commit  [view commit](http://github.com/pyr0ball/pyr0piezo/commit/3f5af8ced7dc1dfc5b8074e8f6127acd8a35957a) 

- updated circuit explanation docs  [view commit](http://github.com/pyr0ball/pyr0piezo/commit/91b72b71a10293e891dcd5d7f01b6684f2775397) 

- Added installation tutorial for MPDM  [view commit](http://github.com/pyr0ball/pyr0piezo/commit/067c4c0df390b468aa43b1285c58c6f5e602a4ed) 

- fixed typo and missing image asset on install page  [view commit](http://github.com/pyr0ball/pyr0piezo/commit/529485f75a239028bec144c34d826c6e769c535d) 

- added a little more info about gettin support to installation page  [view commit](http://github.com/pyr0ball/pyr0piezo/commit/e625f5fcaf89aa806cfd58b865e57ec195017f2a) 

- Fixed links to images in a couple of pages  [view commit](http://github.com/pyr0ball/pyr0piezo/commit/3955912fb1bd1ec780ddd105a04e84ff1cf5a2d8) 

- Added paypal.me donation link to docs site  [view commit](http://github.com/pyr0ball/pyr0piezo/commit/83997a2fab4375cddff9256202e29f0b1f4d4e3f) 

- formatting fix for markdown in pt100 page  [view commit](http://github.com/pyr0ball/pyr0piezo/commit/3b46a42023dd5dc6e368d0758cb93247772f33ad) 

- Code comments/formatting  [view commit](http://github.com/pyr0ball/pyr0piezo/commit/7086002db535978ebb8bbd9deb0b0a25816f8a55) 

- fixed incorrect annotation on one config  [view commit](http://github.com/pyr0ball/pyr0piezo/commit/a44ed2556f393929b5706f03524492a56760e9a8) 

------------------------------------

 *Full Changelog*

- updated readme [view commit](http://github.com/pyr0ball/pyr0piezo/commit/4300c905516beb5e0963778b450ec2463ccec9f0) 

- Autogenerating version number #featureadd [view commit](http://github.com/pyr0ball/pyr0piezo/commit/5cf9c4e94a3b14414befba0423b0cb3273846a4c) 

- updated internal version with latest commit  [view commit](http://github.com/pyr0ball/pyr0piezo/commit/3f5af8ced7dc1dfc5b8074e8f6127acd8a35957a) 

- Merge branch 'develop' into master [view commit](http://github.com/pyr0ball/pyr0piezo/commit/052023eb7947be76b7c6ac7a7e4dcd39207122b4) 

- Merge pull request #64 from loredan/master [view commit](http://github.com/pyr0ball/pyr0piezo/commit/ca0669d7dffa44ea5e437aef12aec28bc39d7829) 

- Added FFC-X-Mot board for v2.1.2  [view commit](http://github.com/pyr0ball/pyr0piezo/commit/9db036fc1ee13d3b5176fb5bf5b92bc0b1705af0) 

- Added eagle source files for SingleDisk PCB adapters  [view commit](http://github.com/pyr0ball/pyr0piezo/commit/6b6d13e08fdaa915b19635e5706014ff1557589d) 

- added configs for new features logic level and pzdet  [view commit](http://github.com/pyr0ball/pyr0piezo/commit/a4a9cb90813fc5e266a67536046f3ae7843fea3a) 

- updated v2.2.0 eagle files with latest library parts  [view commit](http://github.com/pyr0ball/pyr0piezo/commit/2e8d5cba4c94b07c971bc0f6fb4b212f942b47e4) 

- updated eagle parts library to latest  [view commit](http://github.com/pyr0ball/pyr0piezo/commit/83e43f34ae264cc559ccf97175229d012f8606b7) 

- updated eagle project file with latest library urn [view commit](http://github.com/pyr0ball/pyr0piezo/commit/62c459e0dc21a6f95cb10052ce2009102c441938) 

- gave singledisk pcb a bit more flex for better sensitivity  [view commit](http://github.com/pyr0ball/pyr0piezo/commit/0de1676e642282700ff34fe56c29fd853e1f06e2) 

- Merge branch 'master' of https://github.com/pyr0ball/pyr0piezo into develop [view commit](http://github.com/pyr0ball/pyr0piezo/commit/61995934eb96a093d42fb98284abd59c655b2741) 

- Merge branch 'develop' of https://github.com/pyr0ball/pyr0piezo into develop [view commit](http://github.com/pyr0ball/pyr0piezo/commit/76fb8c36310b9d08ca59388e83678511cce2491d) 

- Merge pull request #65 from pyr0ball/develop [view commit](http://github.com/pyr0ball/pyr0piezo/commit/65f941cd0680d61e33342ae1d4a51e85a2202633) 

- added eagle library backup files to gitignore [view commit](http://github.com/pyr0ball/pyr0piezo/commit/d203ce5e9617a2120a04a04697e361f0435a15da) 

- updated gitignore with eagle library temp files [view commit](http://github.com/pyr0ball/pyr0piezo/commit/4c6e21e67ab8cc35e0c6a46edd24b5490e4426cf) 

- updated eagle library with latest parts [view commit](http://github.com/pyr0ball/pyr0piezo/commit/43e04a3e90131085a976a528813d200e5ed1e2d6) 

- Update to README [view commit](http://github.com/pyr0ball/pyr0piezo/commit/82dd63f11111d0ddbd11bed4a46ad8f5200f0623) 

- updated piezoPCB singledisk for better actuation  [view commit](http://github.com/pyr0ball/pyr0piezo/commit/effa5c7d7faf5e5383f9e7b8dcab6c5f0658d752) 

- trying to eliminate those pesky lbr temp files again  [view commit](http://github.com/pyr0ball/pyr0piezo/commit/db0e457450fa9ba14a52c7b514dc4d7800f73a21) 

- updated circuit explanation docs  [view commit](http://github.com/pyr0ball/pyr0piezo/commit/91b72b71a10293e891dcd5d7f01b6684f2775397) 

- Merge branch 'master' of https://github.com/pyr0ball/pyr0piezo [view commit](http://github.com/pyr0ball/pyr0piezo/commit/fd7fa2b3bdc8c2474bbcb2d7e7d2e5c7559e1859) 

- Added separate cmd file [view commit](http://github.com/pyr0ball/pyr0piezo/commit/30afcdd8b7be6f0fd13ab5e50c1eb692173c7a66) 

- Attempt at fixing compile error [view commit](http://github.com/pyr0ball/pyr0piezo/commit/36b6402b2e1bf0a174e935cc42dd0559d939d87c) 

- Separating declaration and definition - volatile [view commit](http://github.com/pyr0ball/pyr0piezo/commit/bf800e99409aa2a77a68f65a6380e21cf10abf8a) 

- More separation of declaration and definition [view commit](http://github.com/pyr0ball/pyr0piezo/commit/60a26ad3f713238cdc536b0302aa6de5a44fa6f2) 

- Added installation tutorial for MPDM  [view commit](http://github.com/pyr0ball/pyr0piezo/commit/067c4c0df390b468aa43b1285c58c6f5e602a4ed) 

- fixed typo and missing image asset on install page  [view commit](http://github.com/pyr0ball/pyr0piezo/commit/529485f75a239028bec144c34d826c6e769c535d) 

- added a little more info about gettin support to installation page  [view commit](http://github.com/pyr0ball/pyr0piezo/commit/e625f5fcaf89aa806cfd58b865e57ec195017f2a) 

- updated gitignore for CAM outputs under Eagle_Files [view commit](http://github.com/pyr0ball/pyr0piezo/commit/1efaf53379f11a3136bee61716f45fb0534af48b) 

- Added support for either 5v or 3.3v operation  [view commit](http://github.com/pyr0ball/pyr0piezo/commit/b1830500647f918d589c5a2789fab86cfa5f2167) 

- updated parts library with new logo and TH parts  [view commit](http://github.com/pyr0ball/pyr0piezo/commit/b4ea4d7b3e801fa4bebc78481b3216e79aae7109) 

- Built pyr0-piezo v2 circuit on a business card  [view commit](http://github.com/pyr0ball/pyr0piezo/commit/d41e24f2eadb59d8c6f5cf00d4713b647d4d98bf) 

- added compiled firmware used on MPDM  [view commit](http://github.com/pyr0ball/pyr0piezo/commit/8838301821af1c50062aa33850ca78bdb6a1e888) 

- Pull latest changes from master into develop [view commit](http://github.com/pyr0ball/pyr0piezo/commit/c4fc40fa818a78b452a2bdc85cb7c610f2daf903) 

- Merge pull request #68 from loredan/master [view commit](http://github.com/pyr0ball/pyr0piezo/commit/c521adccd33b6d8597e7da8c751769d26fd7cbe2) 

- Added code for switching between 3.3v and 5v signal output  [view commit](http://github.com/pyr0ball/pyr0piezo/commit/12f86c971b6423e21b550d0ae3377014a091d48b) 

- Finished business card design [view commit](http://github.com/pyr0ball/pyr0piezo/commit/8d2174d549d7c7d12a626af161ca07902a616246) 

- Formatting [view commit](http://github.com/pyr0ball/pyr0piezo/commit/f2c3843668c0c5cf79aa38b490d3b087d26d91ec) 

- i2c support, not tested #feature [view commit](http://github.com/pyr0ball/pyr0piezo/commit/02d734b177014aa8d2fc55b756e8568df9544931) 

- Added i2c bridge sketch [view commit](http://github.com/pyr0ball/pyr0piezo/commit/57d11c5b97227ff954a04ad26cda8fe61bfe7241) 

- Correct I2C port now used, fixed config and state reply [view commit](http://github.com/pyr0ball/pyr0piezo/commit/46fc068619dfae9bec039a5e430702ed039f5fff) 

- Merge branch 'develop' of https://github.com/pyr0ball/pyr0piezo [view commit](http://github.com/pyr0ball/pyr0piezo/commit/b3cc47daad9a0a4e9e4517dcdfe4aa05ce0ae3bc) 

- Added VCC switch to I2C [view commit](http://github.com/pyr0ball/pyr0piezo/commit/21f7ee25fed4163b46f0cfd30ddc90b16c9d8a50) 

- Fixed links to images in a couple of pages  [view commit](http://github.com/pyr0ball/pyr0piezo/commit/3955912fb1bd1ec780ddd105a04e84ff1cf5a2d8) 

- Added paypal.me donation link to docs site  [view commit](http://github.com/pyr0ball/pyr0piezo/commit/83997a2fab4375cddff9256202e29f0b1f4d4e3f) 

- fixed syntax error in pt100 page [view commit](http://github.com/pyr0ball/pyr0piezo/commit/acb2e7cee714cae4cdbaaf007af572315ee8e1ef) 

- Merge pull request #70 from loredan/master [view commit](http://github.com/pyr0ball/pyr0piezo/commit/ce91ff63ddbf9a93051e909930894cf10b6faba5) 

- Merge branch 'master' of https://github.com/pyr0ball/pyr0piezo into develop [view commit](http://github.com/pyr0ball/pyr0piezo/commit/b45315f3b53e765771f010d0f22c3864423477c9) 

- Serial commands are now case-insensitive  [view commit](http://github.com/pyr0ball/pyr0piezo/commit/2f4e42d34a00b0e58e4ca3b12aa95ce10a417e57) 

- Added user-friendty VCC readings adjustment  Minor fixes to i2c  [view commit](http://github.com/pyr0ball/pyr0piezo/commit/65dbe60c877d7df285dea69503dcf04b4e33f95f) 

- Merge pull request #71 from loredan/master [view commit](http://github.com/pyr0ball/pyr0piezo/commit/1ea927ecd9c4be146695a829b980e3383231ba26) 

- formatting fix for markdown in pt100 page  [view commit](http://github.com/pyr0ball/pyr0piezo/commit/3b46a42023dd5dc6e368d0758cb93247772f33ad) 

- Code comments/formatting  [view commit](http://github.com/pyr0ball/pyr0piezo/commit/7086002db535978ebb8bbd9deb0b0a25816f8a55) 

- fixed incorrect annotation on one config  [view commit](http://github.com/pyr0ball/pyr0piezo/commit/a44ed2556f393929b5706f03524492a56760e9a8) 

- fixed string concatentate issue on version_git.py  [view commit](http://github.com/pyr0ball/pyr0piezo/commit/74eabff95006689712e1e82c747ca5aed931c24f) 

------------------------------------
### v2.3.0 to v2.3.1

#### This is the first Release Candidate version (Finally out of Beta! YAY!)

Changelog updated 2020-09-28

 *Added Features*

- added kitspace integration  [view commit](http://github.com/pyr0ball/pyr0piezo/commit/495ff2ee1fe38884599242dcc36634eb3b7a24e4) 

- added compiled release firmware v2.3.0_b93dbb6  [view commit](http://github.com/pyr0ball/pyr0piezo/commit/61e6a596c0a4908309174289f38c01c64cdf65c1) 

- incremented base version to v2.3.1 for minor additions  [view commit](http://github.com/pyr0ball/pyr0piezo/commit/62e6caf83fb99b464957d7e3f5c2c204d62e32d1) 

------------------------------------

 *Bugfixes*

- Changed logic default to low instead of high  [view commit](http://github.com/pyr0ball/pyr0piezo/commit/b93dbb68085451accdc0d3084de82d6cfd460704) 

- fixed parsing error for git hash injection to version parameter  [view commit](http://github.com/pyr0ball/pyr0piezo/commit/111d7cffe4eb5dbfdd1be5a1a941e324b4bac33a) 

- Added interpreter hashbang to python version script  [view commit](http://github.com/pyr0ball/pyr0piezo/commit/c0527b9aa911cd08bc13ba24900fe4a7d918fcb8) 

- added fallback version parameter. Fixes #73  [view commit](http://github.com/pyr0ball/pyr0piezo/commit/4c7ab3ec36f3003d11f4074fd5810c1f9757bb91) 

------------------------------------

 *Documentation Updates*

- updated changelog for v2.3.0  [view commit](http://github.com/pyr0ball/pyr0piezo/commit/2184ec69ed98b0d6816eb756c8e51f00dbad1deb) 

- added documentation explaining the bypass jumper. #41 complete  [view commit](http://github.com/pyr0ball/pyr0piezo/commit/c2c6e6e64058716c8450b7fead1582038400c443) 

- updated Pyr0-Piezo configuration instructions with new parameters  [view commit](http://github.com/pyr0ball/pyr0piezo/commit/f744b4539adab88ea1fe57933d37eb5f2a81c400) 

- Added I2C Integration page  [view commit](http://github.com/pyr0ball/pyr0piezo/commit/79887395429af3012afaf1fd019a7409c659731b) 

- fixed i2c docs links  [view commit](http://github.com/pyr0ball/pyr0piezo/commit/bda5d75c7e8479f53ca28d67433d4ae362d0b650) 

- added links to MPDM install guide  [view commit](http://github.com/pyr0ball/pyr0piezo/commit/45023ba6625ee76ef757d860ce0474082d88a2f8) 

- added youtube video of the circuit explanation  [view commit](http://github.com/pyr0ball/pyr0piezo/commit/b225d06b29616a5008cbf7ef8757bc4af80369fd) 

- switching to dark theme on docs site  [view commit](http://github.com/pyr0ball/pyr0piezo/commit/44114dbaec4ccfaf7ab76372067c7c02333c5b56) 

- updating 'about' section  [view commit](http://github.com/pyr0ball/pyr0piezo/commit/0f3db0f7ef1fc6b6e7fc1be5fb7af9db893bb313) 

- fixed i2c byteslength for some inputs  [view commit](http://github.com/pyr0ball/pyr0piezo/commit/5581fac1ce19801d3dcbecb35f52f8f8e4bfb9a5) 

- added i2c command syntax to I2C page  [view commit](http://github.com/pyr0ball/pyr0piezo/commit/951c53196d39929bb38a6f85adefca7222eb2c96) 

- Added info for Creality Printhead integration  [view commit](http://github.com/pyr0ball/pyr0piezo/commit/7255c99d183c69ea5b3167a5a330467425aab00e) 

- Added embedded model frames for creality  [view commit](http://github.com/pyr0ball/pyr0piezo/commit/3e0380406c9f340714f92a620bd43f7fd1ccb823) 

- added more detail to firmware update procedure  [view commit](http://github.com/pyr0ball/pyr0piezo/commit/b58bf62e701c77b8429028f22c50fafe6da67320) 

- fixed links and punctuation on firmware update  [view commit](http://github.com/pyr0ball/pyr0piezo/commit/66fbcda4fac84377005ec7e43bed4c96b11be130) 

- fixed typo in VSC extension name  [view commit](http://github.com/pyr0ball/pyr0piezo/commit/0aa790ffb1e4612a271e92326a7b14515cff2a69) 

- added mechanical and pinout drawing for programming jig  [view commit](http://github.com/pyr0ball/pyr0piezo/commit/50ea75049a47e1e9f913863862af414e64945b18) 

- added screenshot for AVRDUDESS procedure  [view commit](http://github.com/pyr0ball/pyr0piezo/commit/a86c3af806a21b7c4436104ae3fecfd145fd0a6f) 

------------------------------------

 *Full Changelog*

- updated changelog for v2.3.0  [view commit](http://github.com/pyr0ball/pyr0piezo/commit/2184ec69ed98b0d6816eb756c8e51f00dbad1deb) 

- Merge pull request #72 from pyr0ball/develop [view commit](http://github.com/pyr0ball/pyr0piezo/commit/4239641fc16ac646b638fa1e66d3afaf1c718f74) 

- added documentation explaining the bypass jumper. #41 complete  [view commit](http://github.com/pyr0ball/pyr0piezo/commit/c2c6e6e64058716c8450b7fead1582038400c443) 

- updated Pyr0-Piezo configuration instructions with new parameters  [view commit](http://github.com/pyr0ball/pyr0piezo/commit/f744b4539adab88ea1fe57933d37eb5f2a81c400) 

- Added I2C Integration page  [view commit](http://github.com/pyr0ball/pyr0piezo/commit/79887395429af3012afaf1fd019a7409c659731b) 

- fixed i2c docs links  [view commit](http://github.com/pyr0ball/pyr0piezo/commit/bda5d75c7e8479f53ca28d67433d4ae362d0b650) 

- added links to MPDM install guide  [view commit](http://github.com/pyr0ball/pyr0piezo/commit/45023ba6625ee76ef757d860ce0474082d88a2f8) 

- added youtube video of the circuit explanation  [view commit](http://github.com/pyr0ball/pyr0piezo/commit/b225d06b29616a5008cbf7ef8757bc4af80369fd) 

- switching to dark theme on docs site  [view commit](http://github.com/pyr0ball/pyr0piezo/commit/44114dbaec4ccfaf7ab76372067c7c02333c5b56) 

- updating 'about' section  [view commit](http://github.com/pyr0ball/pyr0piezo/commit/0f3db0f7ef1fc6b6e7fc1be5fb7af9db893bb313) 

- fixed i2c byteslength for some inputs  [view commit](http://github.com/pyr0ball/pyr0piezo/commit/5581fac1ce19801d3dcbecb35f52f8f8e4bfb9a5) 

- added i2c command syntax to I2C page  [view commit](http://github.com/pyr0ball/pyr0piezo/commit/951c53196d39929bb38a6f85adefca7222eb2c96) 

- migrated hardware files to new location [view commit](http://github.com/pyr0ball/pyr0piezo/commit/95ca33774fb2737be82b4db833843a349c6c9679) 

- added kitspace integration  [view commit](http://github.com/pyr0ball/pyr0piezo/commit/495ff2ee1fe38884599242dcc36634eb3b7a24e4) 

- fixed schematic headers for kitspace [view commit](http://github.com/pyr0ball/pyr0piezo/commit/04ec61d2236a40c88ee2ee617439bded03467bea) 

- added readme for business card, updated kitspace yaml [view commit](http://github.com/pyr0ball/pyr0piezo/commit/425849bbaed78c2e1894da727ce9575c081bd6af) 

- kitspace.yaml link update [view commit](http://github.com/pyr0ball/pyr0piezo/commit/84aa91c5d72aeb504f785e00a8801526f2aaba57) 

- partial update to kitspace yaml and BOMs [view commit](http://github.com/pyr0ball/pyr0piezo/commit/c3f7f86268cf1bb771c9dbd96911a118ecf9d87f) 

- added logo to Standalone pcb [view commit](http://github.com/pyr0ball/pyr0piezo/commit/9581f1b57000172b6337a91a5fef290c78c669eb) 

- Added info for Creality Printhead integration  [view commit](http://github.com/pyr0ball/pyr0piezo/commit/7255c99d183c69ea5b3167a5a330467425aab00e) 

- Added embedded model frames for creality  [view commit](http://github.com/pyr0ball/pyr0piezo/commit/3e0380406c9f340714f92a620bd43f7fd1ccb823) 

- added more detail to firmware update procedure  [view commit](http://github.com/pyr0ball/pyr0piezo/commit/b58bf62e701c77b8429028f22c50fafe6da67320) 

- fixed links and punctuation on firmware update  [view commit](http://github.com/pyr0ball/pyr0piezo/commit/66fbcda4fac84377005ec7e43bed4c96b11be130) 

- fixed typo in VSC extension name  [view commit](http://github.com/pyr0ball/pyr0piezo/commit/0aa790ffb1e4612a271e92326a7b14515cff2a69) 

- added mechanical and pinout drawing for programming jig  [view commit](http://github.com/pyr0ball/pyr0piezo/commit/50ea75049a47e1e9f913863862af414e64945b18) 

- added screenshot for AVRDUDESS procedure  [view commit](http://github.com/pyr0ball/pyr0piezo/commit/a86c3af806a21b7c4436104ae3fecfd145fd0a6f) 

- Changed logic default to low instead of high  [view commit](http://github.com/pyr0ball/pyr0piezo/commit/b93dbb68085451accdc0d3084de82d6cfd460704) 

- added compiled release firmware v2.3.0_b93dbb6  [view commit](http://github.com/pyr0ball/pyr0piezo/commit/61e6a596c0a4908309174289f38c01c64cdf65c1) 

- incremented base version to v2.3.1 for minor additions  [view commit](http://github.com/pyr0ball/pyr0piezo/commit/62e6caf83fb99b464957d7e3f5c2c204d62e32d1) 

- fixed parsing error for git hash injection to version parameter  [view commit](http://github.com/pyr0ball/pyr0piezo/commit/111d7cffe4eb5dbfdd1be5a1a941e324b4bac33a) 

- Added interpreter hashbang to python version script  [view commit](http://github.com/pyr0ball/pyr0piezo/commit/c0527b9aa911cd08bc13ba24900fe4a7d918fcb8) 

- added fallback version parameter. Fixes #73  [view commit](http://github.com/pyr0ball/pyr0piezo/commit/4c7ab3ec36f3003d11f4074fd5810c1f9757bb91) 

------------------------------------

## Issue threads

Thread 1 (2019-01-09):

Address Arduino Code for Auto-Adjust VRef

pyr0ball, 2019-01-09:
Current code for adjusting the comparator stage voltage reference is broken. Need to rework the code for adjusting the resistor ladder, or switch to using PWM + LPF

pyr0ball, 2019-01-09:
Original resistor ladder functionality has been verified working. Possibly will still move to pwm/dac for more grainular control

pyr0ball, 2019-02-12:
Possible code for 10-bit pwm DAC: https://www.avdweb.nl/arduino/adc-dac/fast-pwm-dac

pyr0ball, 2019-02-13:
After testing, no need for 10-bit, analog write works just fine with proper filtering.

Testing (experimentation) shows best frequency response and smoothing (+7mV / -12mV) is achieved with:

10k resistor
3.3uF + 10uF SMD ceramic capacitors

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

Auto-Adjust reconfiguration can be enhanced using these topologies:

- Linear Resistor ladder used to adjust gain on first amp stage
- PWM DAC for adjusting comparator noninverting input
- Adjust V_FOLLOW net to output ~2v for wider adjustment window

pyr0ball, 2019-03-09:
Implementation fixed in https://github.com/pyr0ball/pyr0piezo/commit/2297f152071bde9b9c72eb6032e626e3b168ec5c

Closed 2019-03-09.

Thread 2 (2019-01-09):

Serial input to select sensor profile

pyr0ball, 2019-01-09:
Conceptual feature enhancement:

User can send a command over serial to have the AVR self-configure for a specific kind of piezo sensor, alter voltage range thresholds, etc.

Needs:
 - Acceptable voltage ranges for specific piezo sensors
 - Suggested models / BOM
 - Compatibility request list

pyr0ball, 2019-02-11:
Commit https://github.com/pyr0ball/pyr0piezo/commit/118e8cf7e0f64ea669cd7298c0c62c95fe758189 opens up enough pins to create a serial communication channel back to control board

pyr0ball, 2019-02-19:
[Tutorial on serial input basics](https://forum.arduino.cc/index.php?topic=396450)

pyr0ball, 2019-09-25:
Serial Input has been established, some changes may be required in future but another issue can be opened for those

Closed 2019-09-25.

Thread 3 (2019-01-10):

Arduino Code is too large for Atmega48 (88+ is ok)

pyr0ball, 2019-01-10:
Current sketch uses 5900 bytes, well over the 4kb limit of the mega48.

Refactor using low-level code will be required to fit the sketch on the smaller flash size, or switch to mega88+ may be required

teemuatlut, 2019-03-03:
Hey I saw your project on reddit and browsed this github page for a bit. Is this issue still ongoing for you?

I spent a few minutes making changes and with the serial stuff taken out, I got it to 2426B of progmem and 47 of sram.
I suppose it might be possible to include the serial parser as well considering an empty sketch takes 382B and with `Serial.begin(9600);` added it increased to 1480B.

pyr0ball, 2019-03-03:
I'm actually migrating over to the ATSAMD21E series of MCU's after the beta testing is complete, which has enough memory not to need optimization (though that's not the main reason I'm switching).

Also serial + i2c are going to be required services in the post-beta versions.

I'm trying to keep the code and designs as easy to work with as possible so that other community members can futz around with them.

I do appreciate the offer to help though!

pyr0ball, 2019-09-25:
Closing as the firmware has definitely reached a point where 4K will never be enough

Closed 2019-09-25.

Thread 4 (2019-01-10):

Add support for alternate temperature sensors

pyr0ball, 2019-01-10:
Incorporate circuits for K-type thermocouples and PT100 sensors:

Requires addition of a 4th amp to the circuit. Options:
 - MCP6001 can be switched out for a second LM358.
 - Amp could be installed at the control board side
 - Stack an additional board on top of first using standoffs
   - requires pogo pads or other means by which to connect the boards together, or alternatively a second FFC

pyr0ball, 2019-02-11:
Added PT100 sensor in https://github.com/pyr0ball/pyr0piezo/commit/76f6987b55c771b7c4459a42ef5a0f13f37648e0

pyr0ball, 2019-12-31:
closing, added a long time ago

Closed 2019-12-31.

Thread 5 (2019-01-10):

Multiple Extruder support

pyr0ball, 2019-01-10:
For printers with dual+ extruders, a new design will be needed. Options:
 - Single board, more I/O, larger FFC cable
 - Stacked second board, additional FFC cable in parallel

pyr0ball, 2019-04-17:
Path of least resistance seems to be to stack multiple boards. Single FFC would not be able to carry enough current

Closed 2019-04-17.

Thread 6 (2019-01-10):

Board / Piezo mounts for other printers

pyr0ball, 2019-01-10:
At the moment the only mount I've designed is for the only printer I have one of these installed on. I do have access to a CR-10, Tevo Tarantula, and Davinci Jr, however and will be designing mounts for each of them.

I would also welcome help from the community on this part!

pyr0ball, 2019-02-13:
Received a request from a user to build a mount for the [HyperCube Evo](https://www.thingiverse.com/thing:2937693)

pyr0ball, 2019-12-31:
Closing this as it will be ongoing and new issues should be created for individual platforms

Closed 2019-12-31.

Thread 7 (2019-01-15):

Rewire auto adjust ladder to R-2R configuration

pyr0ball, 2019-01-15:
On advice from a user on reprap forums (dc42) I will be increasing the adjustment ladder resolution by switching from it's current configuration (series ladder) to an [R-2R parallel ladder configuration](https://www.tek.com/blog/tutorial-digital-analog-conversion-r-2r-dac).

This will increase the number of possible values from 5 to 16 using the same number of pins. It should also allow for simplified code

Related to https://github.com/pyr0ball/pyr0piezo/issues/1

pyr0ball, 2019-02-13:
Closing this issue as I've elected to use the arduino PWM output as VRef adjustment: https://github.com/pyr0ball/pyr0piezo/issues/15

Closed 2019-02-13.

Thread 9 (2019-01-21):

USB-Serial programmer board needs DTR pin to program over serial

pyr0ball, 2019-01-21:
Original schematic for this board does not include some required pins. The 20qfn version of the CP2102 does not have a DSR pin required to send proper reset signal to the AVR during programming.

Need to switch to 24qfn or 28qfn and add a couple of extra passive components

References:
http://forum.arduino.cc/index.php?topic=180861.0
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

Closed 2019-01-21.

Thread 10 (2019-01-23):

Hole spacing on Prusa/Anet mount is too small

pyr0ball, 2019-01-23:
When I started rebuilding this mount in Fusion360, I mis-measured the hole spacing as 21mm square from center to center, when in fact the spacing is 23mm (when using the Toranado and a few other more common mounts)

pyr0ball, 2019-01-25:
Confirmed fixed in latest version. Closing

Closed 2019-01-25.

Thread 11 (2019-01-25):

Prusa/Anet Mount needs bearing insert channel

pyr0ball, 2019-01-25:
Currently when attempting to insert the LM8UU size linear bearings into the upper mount slots, there is not enough tolerance to get them in. I'll need to build in a channel/cutout to give them enough space to be installed

pyr0ball, 2019-02-05:
Tested and fixed with https://github.com/pyr0ball/pyr0piezo/commit/7885a101cf0be66efc169e2876df145f5937da05

pyr0ball, 2019-02-08:
Bearing channel needs to be adjusted. Current version causes binding on Drylin bearings due to  lack of support on one side

pyr0ball, 2019-09-25:
fixed

Closed 2019-09-25.

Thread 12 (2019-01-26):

Add overvoltage / reverse voltage protection

pyr0ball, 2019-01-26:
Currently there is a reverse voltage protection diode onboard, but more in-depth analysis will be needed to ensure all voltage entry points are covered.

Currently there is a 0ohm resistor in place of a fuse, but to complete the overvoltage protection, a zener diode is required. [Example](http://www.learningaboutelectronics.com/Articles/Overvoltage-protection-circuit.php)

A quick rough search turned up [this as an optional component](https://www.digikey.com/product-detail/en/PLZ5V1C-G3%2fH/PLZ5V1C-G3%2fHGICT-ND/8031825/?itemSeq=282910988)

pyr0ball, 2019-02-05:
Fixed standalone board in https://github.com/pyr0ball/pyr0piezo/commit/79da9c6468af9ee90bc09aca5c1727b394169f21

pyr0ball, 2019-02-05:
fixed in https://github.com/pyr0ball/pyr0piezo/commit/7885a101cf0be66efc169e2876df145f5937da05

pyr0ball, 2019-02-05:
Accidental closing of wrong issue

pyr0ball, 2019-03-09:
Fixed in https://github.com/pyr0ball/pyr0piezo/commit/79da9c6468af9ee90bc09aca5c1727b394169f21 and https://github.com/pyr0ball/pyr0piezo/commit/070bef876b96773af2c13c0505ce141b0b537d15

Closed 2019-03-09.

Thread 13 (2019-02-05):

Current LDO on standalone does not supply enough power when only getting 5v input

pyr0ball, 2019-02-05:
When the standalone unit is supplied 5v on it's main input, the AVR does not get activated due to low voltage dropout. LDO appears to be responsible, as it requires 6v or more to work properly

[79L05 Datasheet](https://www.ti.com/lit/ds/symlink/lm79l.pdf)

pyr0ball, 2019-02-05:
Options for fixing this issue:

1. Add a bypass jumper pad which will allow the end user to solder a bridge, bypassing the voltage regulator and allowing the control board's 5v to power the sensor
2. Replace the regulator with an LDO regulator at the same current value (max theoretical for the circuit @ 100mA), that can handle 5v input as well as higher (costs 5x as much as the current one)
3. Replace the regulator with an LDO with lower current output, possibly risking dropout

pyr0ball, 2019-02-08:
Added bypass jumper for now.

https://github.com/pyr0ball/pyr0piezo/commit/0b4e0d56df621e5de7ac43b4e4eb7d8816ab22f7

Additional testing required to determine circuit's overall current draw

pyr0ball, 2019-02-15:
After building more units and setting the "brown-out-detection" fuses to 2.7v, this issue has disappeared. Apparently I goofed and set the brownout detection to 4.5v which was the source of the problem

Closed 2019-02-15.

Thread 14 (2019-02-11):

ToDo: Create PCB assembly documentation

pyr0ball, 2019-02-11:
Documents for PCB assembly are needed:

- [ ] DXF simplified drawing of PCB components, front/back
- [ ] component type/value list
- [ ] recommend assembly order
- [ ] PCB reflow thermal profile
- [ ] initial programming / bootloader install
- [ ] firmware update procedure

pyr0ball, 2019-02-15:
Added documentation in commits:
https://github.com/pyr0ball/pyr0piezo/commit/1d17a8dbc9c0e2c366f647574b28ad20244343db
https://github.com/pyr0ball/pyr0piezo/commit/e2399797b8cc4d5ed9e25f0dfded744ae7c06701

pyr0ball, 2019-02-15:
Added PDF exports of all schematics used in boards that have been fabricated: https://github.com/pyr0ball/pyr0piezo/commit/c462b0a3dc5661c0f24a280ded8cff5d5fa49069

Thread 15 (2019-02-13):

Wire V_FOLLOW and Comparator for PWM + LPF adjustment

pyr0ball, 2019-02-13:
This is one part of the solution to https://github.com/pyr0ball/pyr0piezo/issues/1

Experimentation shows PWM DAC is a decent alternative to using the linear resistor ladder for VRef adjustment. Wiring will be fairly straightforward, as shown in the example below:
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

Experimentation showed that the topology best suited to the frequency generated by the Arduino's PWM is by using a 10k resistor, and parallel 3.3uF and 10uF ceramic capacitors. 22uF introduced a resonance waveform, and 10uF did not sufficiently smooth out the ripples.

pyr0ball, 2019-02-15:
Started on https://github.com/pyr0ball/pyr0piezo/commit/2226025830b979959ceab5072745ae53b767f4f4

pyr0ball, 2019-03-09:
Confirmed this method works on breadboard testing. Implemented for Rev.2.x+

Closed 2019-03-09.

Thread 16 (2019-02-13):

Wire Gain Amp for series resistor ladder

pyr0ball, 2019-02-13:
This is a part of the solution to https://github.com/pyr0ball/pyr0piezo/issues/1

Gain for the circuit can be made adjustable by reassigning the linear resistor ladder currently used by the VRef adjustment to the Gain Amp voltage divider.

The current amplification factor is 3, (10k/3.3k), but several values can be created using this topology. I will need to build a test circuit and run some experiments.

pyr0ball, 2019-02-15:
Started work in https://github.com/pyr0ball/pyr0piezo/commit/2226025830b979959ceab5072745ae53b767f4f4

pyr0ball, 2019-02-15:
Since all of these resistors are now the same value, I'll look into replacing individual resistors with a network package

pyr0ball, 2019-03-09:
Confirmed this method works on breadboard. Implemented for Rev.2.x+

Closed 2019-03-09.

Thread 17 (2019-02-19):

Z-Probe sensor output is Active High, should be active low for safety

pyr0ball, 2019-02-19:
The sensor's current firmware is using active-high logic for z-min triggering. For safety, this logic should be inverted as a frayed wire or other connection issue will be apparent and the printer will refuse to move, rather than missing a high signal and causing a head crash or other damage

Closed 2019-02-19.

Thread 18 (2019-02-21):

Create an x-axis breakout board to replace x-gantry motor cover

pyr0ball, 2019-02-21:
This is an enhancement on the FFC version boards that will introduce a replacement for the housing on the x-axis motor on Creality style gantries.

This housing typically holds the x-min endstop in place. The board will replace the housing covering the x-motor's drive gear, and will integrate the endstop and a breakout for the x-motor, while acting as a right angle turn for the FFC chain.

This will have two main benefits:
 - Integration of the x-axis signals eliminates another messy cable
 - an intermediary board allows for two shorter FFC cables which are easier and cheaper to source

pyr0ball, 2019-04-17:
Rev.2.0.1 FFC chain includes this board

Closed 2019-04-17.

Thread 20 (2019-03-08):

Firmware Rev.2.x.x, Analog readings being displayed as 1.00 consistently. Not changing with PWM adjustment

pyr0ball, 2019-03-08:
After fixing https://github.com/pyr0ball/pyr0piezo/issues/19 a new issue showed up, which is that the analog reading serial output is only showing 1.00 regardless of the actual output.

Probing shows 3.84v and 4.22v on V_FOLLOW and VComp respectively

Svatevit, 2019-03-08:
Try Serial.println(VCompRef,2);

foodbandlt, 2019-04-22:
Addressed in #25 if you want to re-enable those debug variables in the future.  Each line of Serial.println takes a crazy amount of flash (up to 4% each in some cases) on the ATmega88.  Crazy.

pyr0ball, 2019-04-23:
@foodbandlt actually could you take another look at it after the merge? Notepad++ on one of my systems was badly configured and may have overwritten some of the whitespace fixes you did, and I had to manually merge, so I could have accidentally deleted that part

Closed 2019-06-27.

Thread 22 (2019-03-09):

Configure MCU for i2c slave device

pyr0ball, 2019-03-09:
Setting the sensor up as an i2c slave will allow to accept input form 3d printer controller as a peripheral device without needing to tie up a UART connection

klcjr89, 2019-03-27:
Have you considered doing a Kickstarter? I really would love to buy one of these boards, as I don't have the time to get the PCBs made and gather the components. I think your product would be the best one of all of the auto bed leveling options out there.

pyr0ball, 2019-03-27:
@klcjr89

It's definitely on my radar, but I want to get the beta (Rev.2.x) finished and validated, and at least start on the firmware for the migration to ARM before I start any crowdfunding, as I want to be sure I can deliver a working product without that usual 3-years-later hooey that usually happens.

I also have a ton of documentation to do, but that's getting worked on in between other development stuff.

Anyhoo, if you're interested in a beta unit, feel free to message me directly or you can post on the discord channel #beta-signup.

Being a beta tester does require some level of expertise and a willingness to put in a little work to iron out the fine details of the project, but if you're up to it, I'd be glad to send you one!

klcjr89, 2019-03-27:
I have alot of 3D printing experience, so I would be interested in a beta unit; I can't seem to be able to join the Discord however, it's not working. I recently launched a Kickstarter myself that ends today: https://www.kickstarter.com/projects/1536120962/pei-coated-flex-plate-system-for-3d-printers/

I think the piezo would be the best probe to use on my surface.

Taylor-Kun, 2019-03-27:
You did a great job on that kick-started video!

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

klcjr89, 2019-03-27:
@Taylor-Kun Thank you for that, but the credit goes to my videographer. He did a professional job.

pyr0ball, 2019-03-27:
@klcjr89 try this link: https://discord.gg/RSuKj7

looks like your kickstarter is doing exactly what I did on my CR-10 but with better magnets. Definitely a fantastic idea. I might even be able to integrate this sensor with your idea if cavities are created in the mount

pyr0ball, 2019-04-23:
Deleted off-topic comments

klcjr89, 2019-04-23:
☹️

pyr0ball, 2020-04-27:
Fixed in #70 and merged into `develop`

Closed 2020-04-27.

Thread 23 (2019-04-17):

Rev.2.x.x - Switch ADC polling to use internal vRef

pyr0ball, 2019-04-17:
Currently the firmware logic doesn't directly account for the VCC input voltage of the circuit, but instead polls only the amp circuit for adjustment data. This has shown to cause instability with the voltage adjustment output.

Switching on the internal vRef and getting VCC polling will allow the ADC logic to be more precise and anticipatory of voltage fluctuations, without getting the big swings that occur from referential polling.

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

pyr0ball, 2019-04-23:
Switching over to the internal VRef will require hardware changes:

- ADC inputs need to be stepped down to 1.1v max, necessitating the addition of a voltage divider for each ADC input
- ARef pin needs to be decoupled with an additional capacitor (100pF - 0.1uF)

Closed 2019-06-27.

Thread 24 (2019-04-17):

Add software hysteresis and reduce analog adjustment adjustment increments

pyr0ball, 2019-04-17:
The current PWM DAC output swings between voltages wildly due to inaccuracies with the ADC inputs, and because of #20 where the internal vRef is not being utilized.

On current Rev.2.0.1/2.1.0 hardware, this issue may be mitigated by reducing the increments that the ADC logic will attempt to adjust the PWM DAC output, as well as adding hysteresis.

Hysteresis can be added easily by subtracting an integer value from the Diff variables.

Lowering the increments that the DAC output will change can be accomplished by dividing the ADJ_COMP and ADJ_FOLLOW variables by a larger value

pyr0ball, 2019-04-23:
Additions created which helped the behavior on breadboard/bench testing, but not with the Atmega88pa and Rev.2.0.1 production board. Closing as an added enhancement, will open a new ticket for the actual bug

Closed 2019-04-23.

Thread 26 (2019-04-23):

Firmware Rev.2.x.x - PWM outputs oscillate randomly without settling on correct voltage

pyr0ball, 2019-04-23:
This behavior was observed on the bench testing platform (using an Atmega2650) until hysteresis and a few other enhancements were added in #24.

Currently those enhancements have not yielded the same results on the Rev.2.0.1 production boards. Screencap of the current PWM output behavior:
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

It's possible the slower clock speed of the At88 vs the At2560 is a factor, as the ADC is getting fewer checks and less able to correct for overshoot compared, or there could be other unforseen factors like PCB layout and capacitor type.

First steps will be to reduce the delay for polling the ADC pins to see if that improves the behavior, other tests will probably reveal other solutions

Closed 2019-06-27.

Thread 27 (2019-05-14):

Add automated thermal compensation control

pyr0ball, 2019-05-14:
As higher temperatures cause a reduction in the effective output of piezo elements, when the sensor is used in an under-bed configuration, the gain of the input must be increased to compensate. As this temperature can be variable, the sensor needs to be able to detect the change and compensate automatically.

This can be accomplished in a few different ways:

 - Direct user input
 - Onboard thermal sensing
 - Input from the printer's controller relaying it's bed temperature measurements

pyr0ball, 2020-01-17:
While this feature is good in theory, in practical use-cases, it's much easier to keep the piezo element away from heating elements that will effect it. From my research, after a piezo element experiences enough heat to cause it's output profile to change, the effect is mostly permanent, which would require either a one-time manual adjustment, or a replacement piezo element.

Closed 2020-01-17.

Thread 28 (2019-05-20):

Separate trigger duration output and trigger reset delay

pyr0ball, 2019-05-20:
Currently the trigger output pulse tied to the piezo interrupt function is partially governed by the delay length of the main loop function. I believe this may be part of what's causing the auto bed level on the Monoprice Delta Mini to prematurely trigger on the second tap. To fix it, I need to separate the actual pulse length out from the loop delay duration, and make sure there are some checks in place that assure the trigger delay function doesn't exceed the length of the loop delay to avoid a premature cutoff.

Closed 2019-06-11.

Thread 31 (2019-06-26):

Eliminate floats for code optimization

pyr0ball, 2019-06-26:
Eliminating floats from the code will free up roughly 30% of the flash. Currently floats are only used for setting voltage levels. This can be converted to millivolts to eliminate the need for floats.

Closed 2019-06-27.

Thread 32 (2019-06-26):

Add logic to automatically adjust thresholds for 3.3v operation

pyr0ball, 2019-06-26:
Currently the initial voltage thresholds set in the firmware are assuming a 5v input. Upon boot, the controller should sense Vin, and adjust thresholds lower if Vin is below a certain threshold

pyr0ball, 2019-09-25:
fixed in f745940904f9e4af4e9a75ff3ffe168a2518b4d0

Closed 2019-09-25.

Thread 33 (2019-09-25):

[FR] Need to add a function or sub-program to calibrate the Atmega internal reference

pyr0ball, 2019-09-25:
**Is your feature request related to a problem? Please describe.**
The method used to sense Vcc relies on the internal 1.1v reference built into the Atmega core. There's minor drift in voltage between IC's

**Describe the solution you'd like**
This can be compensated for in the software by changing the "voltMeterConstant" variable.

Currently this can only be set by changing the constant value in the firmware source, but I think adding a function to update it and save to EEPROM would make the process much less painful.

**Additional context**
Method to calculate the correct voltmeter constant:

```
The reading can be fine-tuned by using a multimeter, and this equation:

scale_constant = internal1.1Ref * 1023 * 1000

where

internal1.1Ref = 1.1 * Vcc1 (per voltmeter) / Vcc2 (per readVcc() function)
```

pyr0ball, 2019-09-25:
Basic function to allow user input added in https://github.com/pyr0ball/pyr0piezo/commit/9e885f316effc105f29027d1b859969f77477851

Closed 2020-05-10.

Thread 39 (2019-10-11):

[FR] Add board revision to silkscreen

foodbandlt, 2019-10-11:
Having the board revision silkscreened on the board will make guessing the board revision from the schematics a thing of the past.  Although I do enjoy going through all of the revision schematics, this is probably necessary.

Closed 2019-10-11.

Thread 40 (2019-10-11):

[FR] Add website URL to board silkscreen

pyr0ball, 2019-10-11:
**Is your feature request related to a problem? Please describe.**
Currently the only branding on the board is the logo. A website would help users find documentation and support if needed

**Describe the solution you'd like**
add docs.pyroballpcbs.com to the silkscreen

**Additional context**
Originally suggested by maxcom

pyr0ball, 2020-01-17:
resolved in board rev 2.2.0

Closed 2020-01-17.

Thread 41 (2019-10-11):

[FR] Add documentation explaining SJ1 solder bridge

pyr0ball, 2019-10-11:
**Is your feature request related to a problem? Please describe.**
Currently SJ1 is only needed for instances when the end-user is supplying <6vDC to the EasyPiezi board.

**Describe the solution you'd like**
 Documentation about what it's for, why and when to use it, and how to use it should be added to the documentation site

**Additional context**
Originally suggested by maxcom

maxcom, 2019-10-11:
I have no idea why you mentioned me here.

pyr0ball, 2019-10-11:
@maxcom My apologies, you have the same username as one of my beta testers under a different platform. I just realized this and removed the links

pyr0ball, 2020-05-13:
Completed in c2c6e6e

Closed 2020-05-13.

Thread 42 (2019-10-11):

[FR] Define "UP" or relative position of the board for documentation

pyr0ball, 2019-10-11:
**Is your feature request related to a problem? Please describe.**
Some users reported confusion as to which orientation of the board is being used when describing features or connections

**Describe the solution you'd like**
Add an explanation and diagram to the docs site defining the usual board orientation.

**Additional context**
Originally suggested by @maxcom

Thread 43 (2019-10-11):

[FR] Add Piezo Disk soldering guide to docs site

pyr0ball, 2019-10-11:
**Is your feature request related to a problem? Please describe.**
Since the beta kits were shipped using bare piezo disks, end-users will need to solder their own wires to it.

**Describe the solution you'd like**
Need to add a guide on how to do this to the documentation site, either with images or a video.

**Additional context**
Originally suggested by maxcom

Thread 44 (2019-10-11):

[FR] Add documentation regarding the integrated PT100 daughterboard

pyr0ball, 2019-10-11:
**Is your feature request related to a problem? Please describe.**
Currently there is no documentation on the PT100 sensor integration

**Describe the solution you'd like**
Create documentation for:
 - PT100 circuit diagrams
 - Hookup guides
 - General explanation of how it works

**Additional context**
Originally suggested by maxcom

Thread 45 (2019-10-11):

[FR] Need documentation explaining what each config parameter does

pyr0ball, 2019-10-11:
**Is your feature request related to a problem? Please describe.**
Currently there's no available documentation explaining what effects changing each parameter over serial will do

**Describe the solution you'd like**
Need a detailed document describing each parameter, what it's effects are, and what implications it has for the sensor behavior

pyr0ball, 2020-05-13:
Added, closing

Closed 2020-05-13.

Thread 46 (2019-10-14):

[FR] PCB pin compatible with arduino nano

AlmightyFrog, 2019-10-14:
**Is your feature request related to a problem? Please describe.**
Custom tailored boards are hard to get.

**Describe the solution you'd like**
A solution would be to separate generic microcontroller part (e.g. use arduino nano) from specific part (LM2902 opamp).
This can be achieved by using DIP components on either breadboard or better simple PCB.

**Describe alternatives you've considered**
An alternative would be design single sided PCB with SOIC to be etched at home.

**Additional context**
Is there a plan or interest in doing such design?
How about current v2.x schematics, is it pretty much stable or subject to change?

pyr0ball, 2019-10-14:
@AlmightyFrog I'd be happy to put together a layout like this if you want to make your own. Is there a particular MCU dev board you have in mind?

The current methodology will likely stay the same going forward, but when I switch over to the ARM/CortexM0 MCU's the circuit will likely be a bit simplified as the SAMD21 MCU I plan to use has a number of hardware peripherals that can eliminate the need for as many external components.

AlmightyFrog, 2019-10-16:
I find this project apealing and would like to test it at some of my printers, but it would be hard to get the specialised boards which also can't be easily extended.

I've had a look at some easy and widely available boards and came to the conclusion, that the Arduino Nano (see features and schematics at https://store.arduino.cc/arduino-nano) would be most likely the best choice.

It is:
- easy to use and flash
- widespread platform
- small form factor
- cheap
- available in both 3v3 an 5v (as you already limit to 8 MHz)

If you compare the schematics, at Nano there is at PB5 an LED attached at the SCK pin but that does not harm and can be ignored.

Having already all pins exposed for easy access, i guess a PCB could spare the test points, also power circuit is already available and therefore obsolete.
Flashing is possible over ISP header or USB-Serial chip onboard, so also that is fine.

What do you think @pyr0ball?
I see some options which have all their own up and downsides:
1. For etching at home, using single sided PCB with big footprints (minimum 0805 SMD for resistors and capacitors and SOIC for chip) would be optimal.
2. For getting people to start on their prototype board, maybe only a easy alignment of components and showing which pins to connect where would be helpful.
3. For getting produced shields for Nano, there the gold standard would be using double sided PCB as this is cheaply available.

Option 1 is my preference to get started.
Option 2 I myself would not use, as I fear issues due to bad contact points using jumper wires.
Option 3 is interesting, but maybe only worth it after some time when it is clear that the layout is really stable.

---
With regards to your switch over to e.g. SAMD21 I get the point of reducing external components, but with a controller like that you also go away from easy available hardware. I'd never had a look at your project if you would use complex circuits or harder to get controllers.
So it would be nice, if at least the AVR ATmega family still would keep at least maintenance support for some time.

pyr0ball, 2019-10-16:
@AlmightyFrog with regards to the switchover to SAMD21, there's several reasons for doing that beyond the reduction in components:
- Futureproofing. The AVR chips are probably going to be around for a while yet, but the ARM chips are getting a lot more popular and nearly as cheap. I ended up landing on the SAMD21 because it actually costs less than the 328pb I currently use in my custom boards.
- Ease of access is improving. SAMD21 is becoming just as easy to get as 328p boards. Look at the Arduino Zero for instance
- Faster processing. the SAMD21 has an internal 24mHz oscillator, which means a lot of aspects of the circuit work faster, which has a secondary effect of allowing me to use cheaper capacitors for the circuit (currently the most expensive passive component)

In regards to your thoughts on the dev-board compatible circuit, There's a couple of things I wanted clarification on:
- Did you want a design that can be attached as a hat for the Arduino Nano from the getgo, or just the Piezo circuit with the appropriate pins broken out into a header that can be connected to?
- With home-etched circuits, are there any caveats I need to be aware of? I've only ever designed with fab houses in mind.
- Do you have an idea of maximum footprint for the board outline? I have a bad habit of making everything tiny, so working to a minimum/maximum board size would be helpful in making a board that anyone can build easily

AlmightyFrog, 2019-10-21:
@pyr0ball
Thanks for mentioning Arduino Zero, I was not aware about that one. Still more expensive than an "first gen" Arduino board, but i guess availability is then no issue.
Only I don't get why you then not go for something like a STM32. They're available in a wide range and are powerful, too.
Even the STM32F103 which you get on the "Blue Pill" boards already have an Cortex M3 @72 MHz (not sure how high you can go with the internal 8 MHz using PLL) and cost only a few bucks. There would also be with stduino an arduino port for it, but I can't tell how complete it is as I used it only for basic I/O so far.

It's a good question whether to go with an Arduino hat or "just" the piezo circuit.
I'd argue it depends on, if you want to try to spread people using it hat might be the way to go, but for flexibility and ease of use i guess second option makes more sense.

As I want to verify first, if your piezo solution would work for my printers second option would be more than enough. Guess main issue is to get the delicate analog section as stable as possible.

For both home etching and isolation routing you should try to not make too small traces. They shall not be too near and it is a no go to e.g. between 0805 pads pull a trace through.
PCB shall be in best case one sided, so you shall try to avoid vias. As that it not always possible it is best practice to only do pairs of vias which do not cross other when you do straight connecting them by (even unisolated) wire.
I'd draft you an example, but didn't use eagle since it was bought by autodesk.

pyr0ball, 2019-10-21:
@AlmightyFrog

Re: SAMD21 vs STM32: For this project, the actual amount of processing power required is very low, since most of the MCU involvement is just balancing the circuit, so having an M3 would be waaaaay overkill. The SAMD21E that I plan to use was down in the ~$1.35 range when I started speccing it out (bare IC) compared to the STM's which were closer to $2.30+. There's a followup project I have that could utilize an M3/4, but for this M0/M0+ is perfectly fine.

I haven't officially called one or the other the "one" yet, so it's still up in the air.

Check out https://github.com/pyr0ball/pyr0piezo/commit/98cc387b20a6d52af0343cddd30effe4b91d37e1 || https://github.com/pyr0ball/pyr0piezo/tree/master/Eagle_Files/Pyr0-Piezo_DIY-Boards for the standalone piezo circuit I just added.

I will have to make a new version for home etching though.

re: Eagle, IIRC you can get a free license as long as you don't need more than one sheet and only make 2-layer boards. All of the designs I've made so far fit within the free license

AlmightyFrog, 2019-10-29:
I've got the free license version of eagle now and had a look at the DIY-Standalone board.

Looks promising, would be fine for fabrication but for home etching/isolation routing it is a game of luck whether the wires "through" the pads of a resistor work or not.
Also soldering (as there is no mask) is then harder. The only point that would not work out most likely is your VCOMP_PWM going through the trig led pads as it is not centered. And also clearance at C19 might be an issue.

It's been a long time since I used eagle, but i will try to recreate a layout for that PCB which fits my needs and test it out.

pyr0ball, 2019-10-29:
@AlmightyFrog I use a managed library that's attached to my account. It allows me to utilize the Push to Fusion 360 with part models as well as make edits to footprints and such.

I'll do some research on how to make that managed library accessible publicly

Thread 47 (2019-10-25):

[BUG] Ready light doesn't turn green upon power up unless piezo is manually tapped.

klcjr89, 2019-10-25:
**Describe the bug**
The ready light on the 2.1.0 beta board doesn't light up unless the piezo element is first tapped.

**To Reproduce**
To reproduce the behavior, the printer is first turned on, the beta board then boots up and ready light flashes, and then remains off until a tap on the piezo element by a finger causes the green light to light up and remain lit and ready to use for a homing or probing procedure.

**Expected behavior**
I expect for the ready light to light up and remain lit after the printer is powered up.

**Printer Used:**
 - Manufacturer:
Creality
 - Model:
Ender-3
 - Control Board:
Azteeg X5 Mini V3 Ethernet
 - Firmware:
Klipper

**Pyr0-Piezo:**
2.1.0 beta board

pyr0ball, 2019-10-25:
Confirmed. This is behavior I've seen on all the 2.1.0 boards I put together but only became apparent in firmware v2.1.3+ IIRC.

@loredan or @foodbandlt just want you guys to be aware as well so if you come across anything in code that might explain that you can let me know. I'm assuming it's something to do with the setup function, *or* there may be a capacitance issue that needs correction in the startup

loredan, 2019-10-25:
I have encountered this problem, but not sure about the cause yet

As a side note, we really should set up a naming convention for these LEDs, so we are not calling them "green" or "ready", but rather something like "power", "warning", "trigger" and "inverted trigger". It's especially important in case of mismatched colors

pyr0ball, 2019-10-25:
@loredan that's especially true as I mixed two batches of RGB 0606's in my container and apparently the colors are rearranged between them.

klcjr89, 2019-10-25:
I called it a ready light since the silksceen layer appears to show as RDY.

pyr0ball, 2019-10-25:
@klcjr89 That's exactly right, but each of the RGB LED's channels correspond to a different function.

At the moment on the Rev.2.1.0's that got sent out:
Red= Power (Vcc input is high)
Green= Calibration Alert
Blue=Trigger (which appears to not be working correctly. Fixing it in 2.2.0)

klcjr89, 2019-10-25:
Oh! had no idea there was a blue led in there too; nice!

pyr0ball, 2019-10-26:
@klcjr89 ok I figured out the issue

Back in v1.x.x firmware, I wasn't using a task scheduler and the reset of the trigger was handled by the main loop. Now it's handled by the interrupt function.

Here's the fun bit. on boot, the trigger LED blinks several times in order to indicate it's starting up, and it's done via inverting a pin by a count which is doubled in the setup function, which makes it always have an even number. What happens if you flip a switch twice? It goes on and stays off. So yeah I just need to add a +1 to the part of the setup code that doubles the blink count flip-flop and that should fix it.

pyr0ball, 2019-10-27:
fixed in https://github.com/pyr0ball/pyr0piezo/commit/f8efc3d192da328ebaa0f9038c133dedaf4f9d0a

Closed 2019-10-27.

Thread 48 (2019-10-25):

[FR] Detect if no piezo element is plugged in to the PCB header.

klcjr89, 2019-10-25:
**Is your feature request related to a problem? Please describe.**
Feature request is not directly related to problem #47, but it would potentially save people from crashes if a piezo wire gets broken or element damaged.

**Describe the solution you'd like**
Upon powerup, the piezo board can interrogate the PCB header where the piezo element plugs into to see if anything is attached. This would be done in a function call that can be later reused, as described below.

The MCU can additionally poll every X amount of seconds or (however long is determined to be best) to verify that a piezo is still plugged in and that a wire or solder joint has not broken. This would cause the user to investigate their wiring to fix it when they realize their firmware cannot home or probe the Z axis, thus eliminating a crash.

pyr0ball, 2019-10-25:
Detecting a piezo disk plugged in is very doable, but it may not be possible to detect whether the disk is damaged. Being able to halt the system if the piezo becomes unplugged is definitely a required safety feature I believe, however.

No polling should be required when using interrupt pins. I'll set up one of the unused pins as a pullup input, and have that get pulled to ground when the piezo is attached. If the piezo is unplugged, the pin will go high and can set an error state that will keep the system in a "triggered" state until the issue is fixed, which should prevent the printer from damaging itself

pyr0ball, 2019-10-25:
Created new board revision v2.2.x for this feature, as it requires changing a header and attaching a new pin to the MCU

pyr0ball, 2019-12-31:
added in a9d9288

Closed 2019-12-31.

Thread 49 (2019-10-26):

[BUG] Serial input appears to be ignored if VERBOSE is not defined

foodbandlt, 2019-10-26:
**Describe the bug**
Title

**To Reproduce**
* Comment VERBOSE out
* Try to send something over Serial In that would have some output, like CONFIG
* There is no response

**Expected behavior**
MCU should send something back over Serial Out, like the current config

**Pyr0-Piezo (please complete the following information):**
 - Pp Version: EasyPiezi
 - Board Revision: [e.g. Rev.2.1.2]
 - Firmware Version: 2.1.4.6

pyr0ball, 2019-10-26:
Confirmed, I've seen this behavior since 2.1.4, but assume it was due to my programmer being broken.

pyr0ball, 2019-10-28:
Only partially fixed, still missing serial feedback while typing

loredan, 2019-10-28:
I still think that feedback is not strictly needed, most serial terminals I've used have feedback built in, just disabled by default

pyr0ball, 2019-10-28:
It's different to every implementation I've ever used, but honestly I just can't figure out how it got disabled, even after reading through the code again

loredan, 2019-10-28:
Not sure it ever was there, at least I don't see anything resembling echo in code prior to my changes

pyr0ball, 2019-10-29:
@foodbandlt @loredan After our testing today, I've not been able to replicate the behavior with the `VERBOSE` flag. I'm assuming it was related to the VSCode environment settings I used when compiling and flashing the beta units I sent out. The issue with feedback is still present, but the board does accept serial input with or without the flag mentioned in this issue. Closing for now

Closed 2019-10-29.

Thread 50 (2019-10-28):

[FR] Automated environment installer

pyr0ball, 2019-10-28:
**Is your feature request related to a problem? Please describe.**
Currently every contributor / user has to set up their own build environment if they want to modify the firmware. This is not easy for many people.

**Describe the solution you'd like**
A script, either interactive or entirely automated, would go a long way in synchronizing these environments

**Describe alternatives you've considered**
a setup guide might also work

**Additional context**
On Windows, this will require either bundling a wget binary, utilizing powershell, and handing the actual install script off to a posix-like environment like MingW64, or some combination of those

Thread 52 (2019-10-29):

[FR] Add Eagle Managed Library to Repo

pyr0ball, 2019-10-29:
**Is your feature request related to a problem? Please describe.**
Currently the parts library used in this project is attached to my personal Autodesk account, and not publicly accessible

**Describe the solution you'd like**
Eagle recently added functionality allowing "shared folders" including managed libraries. Will need to work on integrating this into the project

pyr0ball, 2019-10-29:
I've opened a [forum post on Autodesk's site](https://forums.autodesk.com/t5/eagle-forum/with-introduction-of-quot-shared-folders-quot-can-we-have-a-quot/td-p/9115229) requesting a public share option. Currently it is only possible to share managed libraries via Autodesk accounts, meaning each user/contributor needs to get an email invite from the folder owner to get access

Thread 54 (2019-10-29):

[BUG] RESET config doesn't save back to EEPROM

klcjr89, 2019-10-29:
**Describe the bug**
Sending RESET via a serial terminal resets the config values, but does not store them back to EEPROM, so on the next powerup, the values are not correct.

**To Reproduce**
Steps to reproduce the behavior:
Issue RESET via a serial terminal with 9600 baud rate.

**Expected behavior**
I expected the RESET method to execute and then store the entire config back to EEPROM.

**Pyr0-Piezo (please complete the following information):**
 - Pp Version: EasyPiezi
 - Board Revision: Rev.2.1.0
 - Firmware Version: Latest

klcjr89, 2019-10-30:
Issue is still present even after downloading latest code and reflashing

klcjr89, 2019-10-30:
Fixed in PR #57

Closed 2019-10-29.

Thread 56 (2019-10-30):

[BUG] For VFOL and VCOMP input, parameters don't take immediately

pyr0ball, 2019-10-30:
**Describe the bug**
When sending new configuration parameters over UART, the user either needs to send the command twice, or wait for a period of time (roughly 4-5 minutes) before the new parameter will be reflected in the board's behavior. If the board is reset, using the reset pin and not just power loss, these two parameters get 0'd out and will not work again til that delayed execution time is passed, or new parameters get sent.

**To Reproduce**
Steps to reproduce the behavior:

Send a command to change VFOL or VCOMP over serial while DEBUG is enabled. ADC readings will not change for a while unless the user sends another command editing the same parameter.

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

**Expected behavior**
When a parameter is sent over UART, the changes should be immediate

**Pyr0-Piezo (please complete the following information):**
 - Pp Version: EasyPiezi
 - Board Revision: Rev.2.1.0
 - Firmware Version: v2.1.5

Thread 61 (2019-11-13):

[FR] Add support for either active high or active low logic

pyr0ball, 2019-11-13:
**Is your feature request related to a problem? Please describe.**
Back in #17 we switched the probe to having active low logic (following the endstop standard) however, many boards that have a dedicated "probe" input seem to have a hardware pullup resistor attached to the logic pin. This means that (with the current scheme of trigger logic) even if the probe board is disconnected, the trigger logic still shows as "open"

**Describe the solution you'd like**
As this is a hardware pullup on the control board side, this sensor needs to be able to accommodate both logic schemes. This will necessitate changing the trigger output function to be invert-able, as well as introducing a new serial input to invert the logic

pyr0ball, 2019-12-31:
fixed in a9d9288

Closed 2019-12-31.

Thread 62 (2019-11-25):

[MOUNT] ADIMLab Gantry-S

ETE-Design, 2019-11-25:
**Is your printer similar to any that currently already have support?**
Like the Ender-3 Just a smaller cover / fan also screws to hold it is on the top

**What mounting scheme do you plan to use?**
Choose between: On-Printhead

pyr0ball, 2019-12-02:
@ETE-Design Any chance there are sources or models for the gantry carriage?

If not, I'll need to get one or have you take measurements (or make a dummy model if you're capable)

ETE-Design, 2019-12-02:
Sorry, no models aviable :-( But can take pictures, and deliver all the messurements you need :-) BTW. Is it possible to get a sample, cause I have the only rights to sell the Gantry-S in EU :-)

pyr0ball, 2019-12-03:
@ETE-Design The boards are still very much in beta, so if you don't mind working with an unproven board, I can work that out with you. DM or @ me on the discord and I'll coordinate with you.

re: mount design, pics with measurements is a good start. Any chance we could reach out to the manufacturer for a 3D model? That would make the process a lot easier and faster.

pyr0ball, 2019-12-05:
First draft of the mount for this model has been posted: https://a360.co/34VN7gC

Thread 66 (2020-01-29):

[FR]Reprap 2 and 3 Configuration

Afteraffekt, 2020-01-29:
Rerap 2 and 3 firmware configuration data missing.

pyr0ball, 2020-01-29:
👍 Will get documentation written once I have a chance to review with one of the beta testers who uses RepRap

Tinchus2009, 2021-06-02:
Any update on this? I use reprap 3.X and I would like to have this docs

pyr0ball, 2021-06-02:
I don't currently have a reprap capable printer to test and make instructions with, but I'd be happy to include documentation if I can get some details about setup from someone who uses it more regularly.

One of my beta testers provided a little snip he used to set up his ezpz:
```GCODE
;M558 P8 F4200 T7000 H10 I1                                  ; Z probe type to PIEZO and the dive
```

gueee, 2023-01-21:
Here's my config running on the following hardware/firmware:
Board: Duet 2 WiFi (2WiFi)
Firmware: RepRapFirmware for Duet 2 WiFi/Ethernet 3.4.0 (2022-03-15)
Duet WiFi Server Version: 1.26
`
; Z-Probe
M574 Z1 S2                                         ; Set endstops controlled by probe
M558 P8 C"!zprobe.in" H3 F2600 T9000 	   	   ; Set Z probe type mini ir sensor
G31 P500 X0 Y0 Z0                       ; Set Z probe trigger value, offset and trigger height
M557 X25:275 Y25:275 S50			   ; Define mesh grid
`

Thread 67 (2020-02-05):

[FR]5v and 3.3v option using LM317

Afteraffekt, 2020-02-05:
LM317 should only take an extra pin. Check to see if it can be fit into the existing footprint.

pyr0ball, 2020-02-05:
Using a combination of 3x resistors with an LM317, voltage adjustment can be made by switching a pin on the MCU from INPUT (high impedance) to OUTPUT-LOW, on the R2 side of the voltage divider used to set the regulator's output.

Will do research on parts cost

Closed 2020-05-10.

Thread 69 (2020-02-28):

[MOUNT] Railcore II ZL/ZLT

EmilyBarbour, 2020-02-28:
**Is your printer similar to any that currently already have support?**
HEVO

**What mounting scheme do you plan to use?**
on print-head

**Additional context**
Corexy printer
Fusion model for printer on this page along with other info.  https://railcore.org/hardware/

pyr0ball, 2020-02-28:
Thanks for putting that request in! I've already started working on an under-bed solution for this printer. It will require adding a "padding" material between the bed plate and the Z Yokes, like a rubber or felt grommet, or a compact spring perhaps.

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
https://a360.co/39bEYqz

If desired, I can also work on an on-head version. Just let me know what works best for you

notacoat, 2020-02-28:
This works! Thanks!

pyr0ball, 2020-02-28:
I've added a rubber grommet as well as a small printed piece to assist with actuation:
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

pyr0ball, 2020-02-28:
@notacoat I realize you'll probably need boards to test this integration method. Are you comfortable coordinating over Discord for that?

Do you want to procure your own boards or have me send you some?

For this integration, you'll need 1x EasyPiezi V2.2.0 or later, and 3x of the SingleDisk Adapter boards.

I'm happy to keep this issue open til you've tested it, but you can close it any time if you feel like it's done

notacoat, 2020-02-29:
@pyr0ball hey, I’d love to help out w testing, but I’m super busy at the moment and won’t have time to at least for a couple weeks.  If you pop into the Railcore discord, there would be a lot of interest in, I bet

pyr0ball, 2020-03-05:
@notacoat awesome, thanks for the tip!

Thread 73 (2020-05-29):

PP_VERSION not defined

Tupptupp, 2020-05-29:
Firmware only compiles in the arduino IDE when I add:

`#define` PP_VERSION 230`

at the top of
"Pyr0_Piezo_Sensor_v2.x.x.cpp"
and
"pP_i2C.cpp"

pyr0ball, 2020-05-29:
This tends to happen when compiling using Arduino IDE or other methods than PlatformIO, or if the user doesn't have python installed and available via the system PATH

There should be an `#ifndef` field to handle this cleanly

pyr0ball, 2020-06-15:
Fixed in 4c7ab3e

Closed 2020-06-15.

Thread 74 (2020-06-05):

[FR] Add motor stall detection to FFC cable chain

pyr0ball, 2020-06-05:
As we're already introducing an MCU nearby the stepper motors, it wouldn't be too difficult to implement a current monitoring circuit that could be tuned to detect stalls and jams.

The circuit would simply need a small-value resistor, or even a serpentine trace with a known resistance, and two ADC pins, or a differential amp circuit and one ADC pin, to detect current spikes, which could then be relayed to the main MCU over I2C

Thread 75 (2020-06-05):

[FR] Add E-Mot header to FFC-X-Mot board

pyr0ball, 2020-06-05:
Currently the FFC cable chain only supports Direct Drive extruders (on-head), but it would be fairly trivial to add a second stepper header to the X-Motor board to allow users to utilize the same PCB for extruder steppers that live on the same mount as the X-Motor (as in the Creality Ender3/CR-10 family)

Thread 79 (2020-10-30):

[FR]Klipper-config.md Lost?

Zero-Grav, 2020-10-30:
**Is your feature request related to a problem? Please describe.**
A clear and concise description of what the problem is. Ex. I'm always frustrated when [...]

**Describe the solution you'd like**
A clear and concise description of what you want to happen.

**Describe alternatives you've considered**
A clear and concise description of any alternative solutions or features you've considered.

**Additional context**
Add any other context or screenshots about the feature request here.

pyr0ball, 2020-10-30:
I need s bit more info to go on here. If you're requesting a firmware configuration page for Klipper, there's nothing special about it as of yet, just set the input pin and zero offsets. Once Klipper introduces menu options for configuring the sensor, and there's gcode around it, I'll flesh out a full page on it.

Zero-Grav, 2020-10-30:
Thanks for your answer.
So this thing can only be used as a Z endstop in the klipper？

pyr0ball, 2020-10-30:
It can be used as a probe as well, you just won't be able to configure the sensor's settings through Klipper till they add support for that.

This is veering off a bit into support territory, so if you need help with getting a piezo sensor set up, you should reach out through the Discord channel or the support email: support@pyroballpcbs.com.

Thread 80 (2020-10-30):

[MOUNT]Voron2.4or1.8orZero

Zero-Grav, 2020-10-30:
**Is your printer similar to any that currently already have support?**
Please list any similar printers that already have Piezo mounts

**What mounting scheme do you plan to use?**
Choose between: On-Printhead, Under-Bed, Gantry-Mount, or Other [if Other, please describe]

**Any existing mounts with public links?**
Create a bullet-point list of any links to mounts similar to what you need, for example, from Thingiverse, TinkerCAD, GrabCAD, etc.

**Describe alternatives you've considered**
A clear and concise description of any alternative solutions or features you've considered.

**Additional context**
Add any other context or screenshots about the feature request here.

pyr0ball, 2020-10-30:
@Zero-Grav please edit this request and fill out each section fully

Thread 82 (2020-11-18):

BLV MGN Cube (CoreXY type) under bed

DarkTerritory, 2020-11-18:
**Is your printer similar to any that currently already have support?**
It may be similar to one of the existing CoreXY designs, but the mounts are different

**What mounting scheme do you plan to use?**
Under Bed

**Any existing mounts with public links?**
Unknown. I can supply photos of the existing mounts if that helps.

**Describe alternatives you've considered**
Unknown

**Additional context**
Unknown

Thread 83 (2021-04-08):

Board burned out

garyriet, 2021-04-08:
Good morning
I was working with my board and it blew out. Was running 9v thru it

pyr0ball, 2021-04-09:
@garyriet could you provide a little more detail about what happened and how?

garyriet, 2021-04-09:
I was testing the board connected to a buck converter set to 9v dc which was connected to my external power supply 13.8v dc.   All voltage measured using a fluke 87 multimeter. Connected board to power and to 4 27mm piezo discs.
Turned power on and was testing for about 5min when I smelled burning, shut power off and found the smell was originating from the board.  Discounted board and measured power it was still at 9v. Reconnected board and it would not power on
Gary

pyr0ball, 2021-04-09:
Can I see a picture of the wiring harness (with pins annotated if possible), as well as a high-res photo of the top of the EzPz board?

garyriet, 2021-04-09:
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

garyriet, 2021-04-09:
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

garyriet, 2021-04-09:
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

garyriet, 2021-04-09:
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

pyr0ball, 2021-04-10:
Thanks for sending a bunch of angles, that really helps!

can I see where this is being plugged in on the controller side?
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

pyr0ball, 2021-04-16:
just checking in to see if you still needed help with this?

garyriet, 2021-04-16:
Yes I do.  Sorry was busy with work.

Gary Rietmann
Cell: (609) 276-1559

Sent from my iPhone

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

pyr0ball, 2021-04-16:
@garyriet I've deleted your previous comment as it contained personal information. Please keep in mind that this is a public forum, and it's generally inadvisable to post contact information in a way that's visible to anyone (bot spammers included)

Can you read the above messages and get back to me about how the board was connected?

garyriet, 2021-04-16:
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

garyriet, 2021-04-16:
It was connected in place of the precision piezo board with DuPont connectors

pyr0ball, 2021-04-16:
I'm really sorry to keep asking,  but I need a better idea of what you connected and where at both ends.

A simple drawn wiring diagram would be helpful, or a complete picture of the entire connection chain.

garyriet, 2021-04-17:
Sure I'll do a drawing morning

garyriet, 2021-04-17:
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

garyriet, 2021-04-17:
Sorry I don't have Visio at home

pyr0ball, 2021-04-20:
That's perfectly alright @garyriet

I'll try and reproduce the issue and let you know what I find out

garyriet, 2021-04-29:
Any update?

pyr0ball, 2021-04-29:
Haven't been able to set up a rig to reproduce just yet, RealJob™ has been keeping me late a lot the last couple of weeks.

I've got an idea what might have caused it but need to try out your wiring scheme to confirm.

garyriet, 2021-05-30:
?? Any info?

pyr0ball, 2021-06-01:
Sorry for the delay, I haven't been able to spend any appreciable time in my lab since the pandemic began, and now that I can get back in, I've had a backlog of high-priority stuff keeping me busy.

Here's what I know so far: There's a red circle around the problem
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

What you can see here is a blowout on the GPIO region of the Atmel MCU. What this means is that too much current or voltage was applied to one of the sensor's sensing, or output pins. Determining the cause of this is usually difficult, but most often is caused by user error (something getting connected to the wrong pin).

In your case, there's  a possibility that an over-voltage potential was created with the wiring scheme you used. In most electronics, it's a good idea to connect the ground planes of all separated electrical devices together, to avoid this problem. From the wiring scheme you provided, the ground wire between your main power supply and the ground on the input to your controller could have caused the sensor board to act as a ground-return, blowing it out. This is still considered user error, but this is also something that can be guarded against in my design, which I didn't think to add protection for.
The wiring scheme you showed me is missing a wire (indicated by a red line here) between the sensor and the ground on the controller.
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

I haven't had a chance to test this theory yet, and need lab time to do so

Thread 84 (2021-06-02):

[MOUNT]

Tinchus2009, 2021-06-02:
**Is your printer similar to any that currently already have support?**
Please list any similar printers that already have Piezo mounts

Not that I know. My printer is a coreXY style, there is no info on the website, the page belonging to it it is empty

**What mounting scheme do you plan to use?**
Choose between: On-Printhead, Under-Bed, Gantry-Mount, or Other [if Other, please describe]

still not decided

**Any existing mounts with public links?**
Create a bullet-point list of any links to mounts similar to what you need, for example, from Thingiverse, TinkerCAD, GrabCAD, etc.

No

**Describe alternatives you've considered**
A clear and concise description of any alternative solutions or features you've considered.

**Additional context**
Add any other context or screenshots about the feature request here.

What I need to know in order to haelp me decide installation is to know this extra information: my printer has an enclosed heated chamber, it can reach upto 200 degrees celsius, can the piezo ant its mounting stand this temperature?

pyr0ball, 2021-06-02:
If you just want some ideas of how to implement on your printer, have a look at the Railcore integration: https://docs.pyroballpcbs.com/mounts/core-xy/railcore-ii/

Re: Heated chamber - Likely you'll start experiencing reduced sensitivity around 80°C, which generally can be compensated for using configuration. Above that, you'll need to enhance the piezo elements somewhat, either by increasing the size of the elements used, or by providing some insulation, or building your enclosure such that the mechanical force of the nozzle touch is translated outside the heated area. Using a standard piezo disk in a 200°C chamber will likely result in serious signal suppression.

That's a problem that may be able to be overcome, however. While signal from the piezo elements would be suppressed, they would not be totally eliminated. I would need to change a couple of resistors on the sensor, but I believe I could modify the circuit to handle a much higher gain input for this scenario.

Anyhoo, if you'd like to explore options for a custom board or circuit, please feel free to reach out direct on Discord or support@pyroballpcbs.com

Closed 2021-06-02.

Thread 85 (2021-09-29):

[MOUNT] Ultimaker 2+

svpcom, 2021-09-29:
**Is your printer similar to any that currently already have support?**
It similar to railcore-ii (core-xy geometry)

**What mounting scheme do you plan to use?**
I'll prefer Under-Bed, but I have some doubts about heat from bed (for ABS bed heated up to 100C when piezo sensor temperature limit < 60C) and vibration from bed when it do Z-moves.

**Any existing mounts with public links?**
N/A

**Describe alternatives you've considered**
Possible variant to mount sensor on print head, but it also has issues with temperature.

**Additional context**
Do anyone have success with installing piezo z-probe to Ultimaker2+ ?

pyr0ball, 2021-10-03:
If you can provide some CAD sources for the UM2 or your own printer, that will help speed the design process for this.

Underbed is how I would typically approach this kind of printer, and the lovely thing about Piezo probing, is you don't necessarily need the piezo element pressed up against the hot parts. As long as mechanical force is applied when the nozzle touches the bed, it should work. Even sharp z-movements should be tuned out by the signal processing circuitry, assuming you're getting a decent mechanical actuation of the piezo element.

Underbed has one big downside, which is that the center of the heated bed will be less sensitive, due to flex in between the mounting points. If you've added support such that the center of the bed is more rigid, this should be a non-issue. Alternatively, you can have piezo's mounted at either end of the X-axis gantry arm, or combine underbed with an on-head element.

Keep in mind, this sensor can work with any number of piezo's hooked up in parallel, and you only need the one EasyPiezi. However, the longer the wire from the piezo element is, the more electrical interference and parasitic inductance will affect the signal.

Let me know what you think, and if you have any other thoughts or ideas~

svpcom, 2021-10-03:
CAD files (hardware design for UM2+ is open-source):  https://github.com/Ultimaker/Ultimaker2ExtendedPlus

The table is on three springs, so I'm thinking of placing the piezo sensors underneath. Will the sensor work if it experiences constant spring pressure? That is, a bolt will pass through the drilled sensor, which tightens the spring on which the edge of the table rests.

When printing with abs plastic, the table temperature is about 100C. The table is thermally insulated in the bottom, but inside the closed volume the iron platform to which the table is attached (through 3 bolts and springs) will still heat up after a while. Will this affect the performance and / or lifespan of the sensors?

pyr0ball, 2021-10-04:
> Will the sensor work if it experiences constant spring pressure?

Yes assuming the polarity is correct, you can even pre-tension the piezo and pick up the "relief" motion if you hook it up backwards

> a bolt will pass through the drilled sensor

You can certainly do this and make it work, but I don't recommend using drilled discs. You'll get much more consistent results by bending the disk across it's diametric center by allowing one side of the disk to be free moving, and the other statically mounted. I build a little PCB that uses 12mm disks that produces the same signal to noise ratio as a 27mm disk. You can find those up on my site, or you can use the sources in the hardware section of this repository to send out to JLC or another fab house if you'd like to build your own.

Any design I do will likely not include drilled discs, unless specifically requested

> Will this affect the performance and / or lifespan of the sensors?

Yes and no. Piezo elements have a particular behavior when it comes to heat, which is that their sensitivity is reduced as more heat is applied. That signal degradation is partially elastic, partially plastic. An analogy that fits is bending a piece of wire. If you deflect a copper wire a small amount, it will return to its original shape, which is an "elastic deformation", but if you bend it further, it will stay in it's deflected state, which is a "plastic deformation". The piezo elements' signal output has a similar effect with heat. After a certain temperature, the signal suppression becomes permanent, but below that threshold, it's elastic. That threshold is different between all elements, so you'll have to test with the ones you've got to find out how much heat they can take.

There's an upside to this! This sensor has the ability to increase it's input signal gain on the fly, so even if the signal from your piezo elements is suppressed, it can be boosted by the sensor to a certain extent. It's also possible to increase the gain beyond the 11x limit of the software, but that would require changing a resistor on the board. If your particular setup requires a higher input gain, and you don't want to do your own, I can rework a couple of units for you.

Another way to address that issue is to migrate the piezo elements to the underside of the springs rather than being pressed up against the bed itself.

> CAD files (hardware design for UM2+ is open-source): https://github.com/Ultimaker/Ultimaker2ExtendedPlus

Ah thanks, I'd forgotten that! I'll take a peek when I've got some free time this week and let you know what I think

pyr0ball, 2021-10-04:
I had a look, and I'm fairly certain a technique like [this one](https://www.thingiverse.com/thing:4836261) will work for the UM2

I'll get something knocked together when time permits!

svpcom, 2021-10-04:
@pyr0ball What do you think about using of ceramic piezo rings like that https://aliexpress.com/item/32871471778.html instead of piezo disks? I'm planning to pass bolts with springs via them.

pyr0ball, 2021-10-05:
The mechanical quality factor on those might be an issue, as I believe these are primarily used for ultrasonic transducers. If I'm making a correct assumption (cus I've never actually tried one of these) it would be kinda like trying to turn a gear reduction box from the output side.

The listing does say it's capable of pressure and vibration sensing, so it's very possible that could work.

I could be completely wrong about that tho, and now I know these exist at that price point I'm definitely gonna grab some to test with! I'll have to see what kind of mechanical requirements these have for actuation. It's very possible that you could just stick these between the bed knurled nuts and the bed platform and you might get a signal if it works how they say.

If you've got an oscilloscope handy and would be up for trying out some tests with my guidance, I can probably give you a pretty solid idea of what they need to work.

pyr0ball, 2021-10-05:
@svpcom Here's a use-case very similar to the UM2 that's utilizing my SingleDisk adapters:
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

I don't think the UM2 has any other mounting holes adjacent to the bed leveling screws, so we may need to resort to an adhesive or something similar for that kind of mount

pyr0ball, 2021-10-06:
Started working on this, and it looks like there *are* mounting holes I can utilize on the UM2! What I don't know is whether they're threaded or not.
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

Can you confirm for me? If they're not threaded you'll likely need a nylock nut to keep them in place

svpcom, 2021-10-06:
They are not threaded. They are intended for the initial leveling of the table during assembly

pyr0ball, 2021-10-06:
do you think they could be used with a nylock nut on the other side?

Alternatively, I could design a mount intended to be used with some 3M adhesive tape (the wall mount kind) instead?

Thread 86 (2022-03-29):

[MOUNT]

calebols, 2022-03-29:
**Is your printer similar to any that currently already have support?**
Please list any similar printers that already have Piezo mounts
I couldn't find any when searching google or specifically Thingiverse

**What mounting scheme do you plan to use?**
Choose between: On-Printhead, Under-Bed, Gantry-Mount, or Other [if Other, please describe]
I'd like to mount this to the printhead but I'm open to suggestions.  I currently have a 3-point bed leveling system in place if that makes a difference.

**Any existing mounts with public links?**
Create a bullet-point list of any links to mounts similar to what you need, for example, from Thingiverse, TinkerCAD, GrabCAD, etc.
There are none that I could find.  I saw 1 for a hemera but for a completely different printer that used linear rails instead of the aluminum extrusions found on an ender.

**Describe alternatives you've considered**
A clear and concise description of any alternative solutions or features you've considered.
Other than going with a different ABL system, I'm not sure what alternatives there are.  The biggest "alternative" I've considered was finding a way to put the piezo's under the bed but I've not figured out how to use them with the bed springs as the bed springs have so much tension that I would think they would always be triggered.

**Additional context**
Add any other context or screenshots about the feature request here.
So, I didn't see a place to specify above but I've got an original Ender 3 with an E3D hemera mount utilizing the new REVO nozzle ecosystem.  As mentioned above, I did switch out the 4-point bed leveling screws with 3-point bed leveling screws.  I don't think it will matter for the mounting but I've got an BTT SKR Mini e3 v3 board installed and I'm running Klipper on a Raspi 3b+.

Thank you in advance for any help!

pyr0ball, 2022-03-30:
With something like the Hemera, you'd probably be better off going with [the under-bed mount](https://www.thingiverse.com/thing:4836261) just due to the inertia involved with those extruder.

If you wanted it on-head still, I'd probably recommend switching to MGN rails to address the stability issues that might crop up

calebols, 2022-03-30:
Thank you for that...I'm not sure how I missed that link!  Unless it was because I had waaayyy too many tabs open while searching :).  I'll give the under-bed mounting a try and see how it goes.  Thanks again!

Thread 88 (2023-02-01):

[MOUNT]

jcortenbach, 2023-02-01:
Hi there!

I'm incredibly impressed by your ABL solution!

I own an Ender 3 V2 with a Biqi H2 V2S Revo hotend.

Do you foresee any compatibility with my setup? An inder-bed soluton sounds most elegant by I'm open to anything. I'd also be willing to change the extruder for a non-revo based variant!

loredan, 2023-02-01:
I own Ender 3 Pro with stock hotend, I've used a hotend mount for some time, but it interfered with a replacement part cooling I wanted to install, so I switched to an underbed one, this one in particular: [https://www.thingiverse.com/thing:4836261](https://www.thingiverse.com/thing:4836261). It didn't really work out, I think 3d printed levers have deformed and lost pre-tension after a while, I replaced those with a metal ones, made from a metal ruler, washers and M3 bolts (see attached picture), and after some tuning it works very well. There are a couple of issues though, probably because ruler was very stiff, I had to crank sensitivity very high, so probe can trigger if I simply bump the table, and piezos pick up a lot of noise from Z axis, so I had to slow down probe to 5 mm/s to avoid false triggers.

Also, we mostly discuss this kind of stuff in Discord, it's easier to do there

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

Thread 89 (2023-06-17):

[MOUNT] FlyingBear Reborn 2

jmacato, 2023-06-17:
**Is your printer similar to any that currently already have support?**
I'm not sure but the 4 springed Ender 3 beds seems to be the closest?

**What mounting scheme do you plan to use?**
Under-Bed

**Additional context**
STEP file for the 3D printer:
[flying-bear-reborn-2.zip](https://github.com/pyr0ball/pyr0piezo/files/11778312/flying-bear-reborn-2.zip)

Closed 2024-04-23.

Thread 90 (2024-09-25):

doc-site down & some Q's

hannpet, 2024-09-25:
I stumbled upon your project, here is some feedback:

- https://docs.pyroballpcbs.com/ sadly seems to be down!
- Where can I buy those Boards? Maybe a link to PCBway or Aliexpress or similar?
- If I want to connect 4 Piezo-rings (underbed), can those be connected in parallel with a 10k Resistor each (like the PrecisionPiezo-Board does it), or is it necessary to use 4 distinct boards because there is more smartness involved?
- Thank you so much for this great project, please keep it alive!🤞

pyr0ball, 2024-09-25:
Sorry about the docs site, my home server suffered a massive hardware failure recently and I've been a little bogged down in recovering all of the webserver stuff. Thankfully all of the docs exist in this repo!

https://github.com/pyr0ball/pyr0piezo/tree/master/docs

You can either read them directly using a markdown viewer, or by building and deploying with mkdocs

Parallel works with a single board!

I still have a buttload of v2.3.2 boards floating around but all of my webserver stuff is toasted. If you really want one of these, we'll work something out.

If you don't need a compact version, you could build one yourself using the business card or mini variations. The board files for those are all in the repo as well if you want to source your own:

https://kitspace.org/boards/github.com/pyr0ball/pyr0piezo/pyr0-piezo%20z-probe%20standalone%20module/
https://kitspace.org/boards/github.com/pyr0ball/pyr0piezo/pyr0-piezo%20z-probe%20business%20card%20diy%20module/

hannpet, 2024-09-26:
Thanks für the reply! Too bad what happened to your server, that is really
painful.

So now I have read myself a little bit into the topic and got kind of
intrigued...
I think I'll try to hook up the Piezo-Rings to a breadboard with a rp2040
or esp32 and ask chatGpt to write me a MicroPython script to do the
sensor-autotuning.... it's probably going to be epic failure, but I kind of
feel like playing around a little bit 🙂

I'll definitely get back to you when I'm about to order a finished product,
thanks a lot Alan for the offer to supply one from your stack.

Am Mi., 25. Sept. 2024 um 20:01 Uhr schrieb Alan Weinstock <
***@***.***>:

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

pyr0ball, 2024-11-20:
Just a heads up, the docs site is back online at https://docs.pyroballpcbs.com

Closed 2024-09-27.

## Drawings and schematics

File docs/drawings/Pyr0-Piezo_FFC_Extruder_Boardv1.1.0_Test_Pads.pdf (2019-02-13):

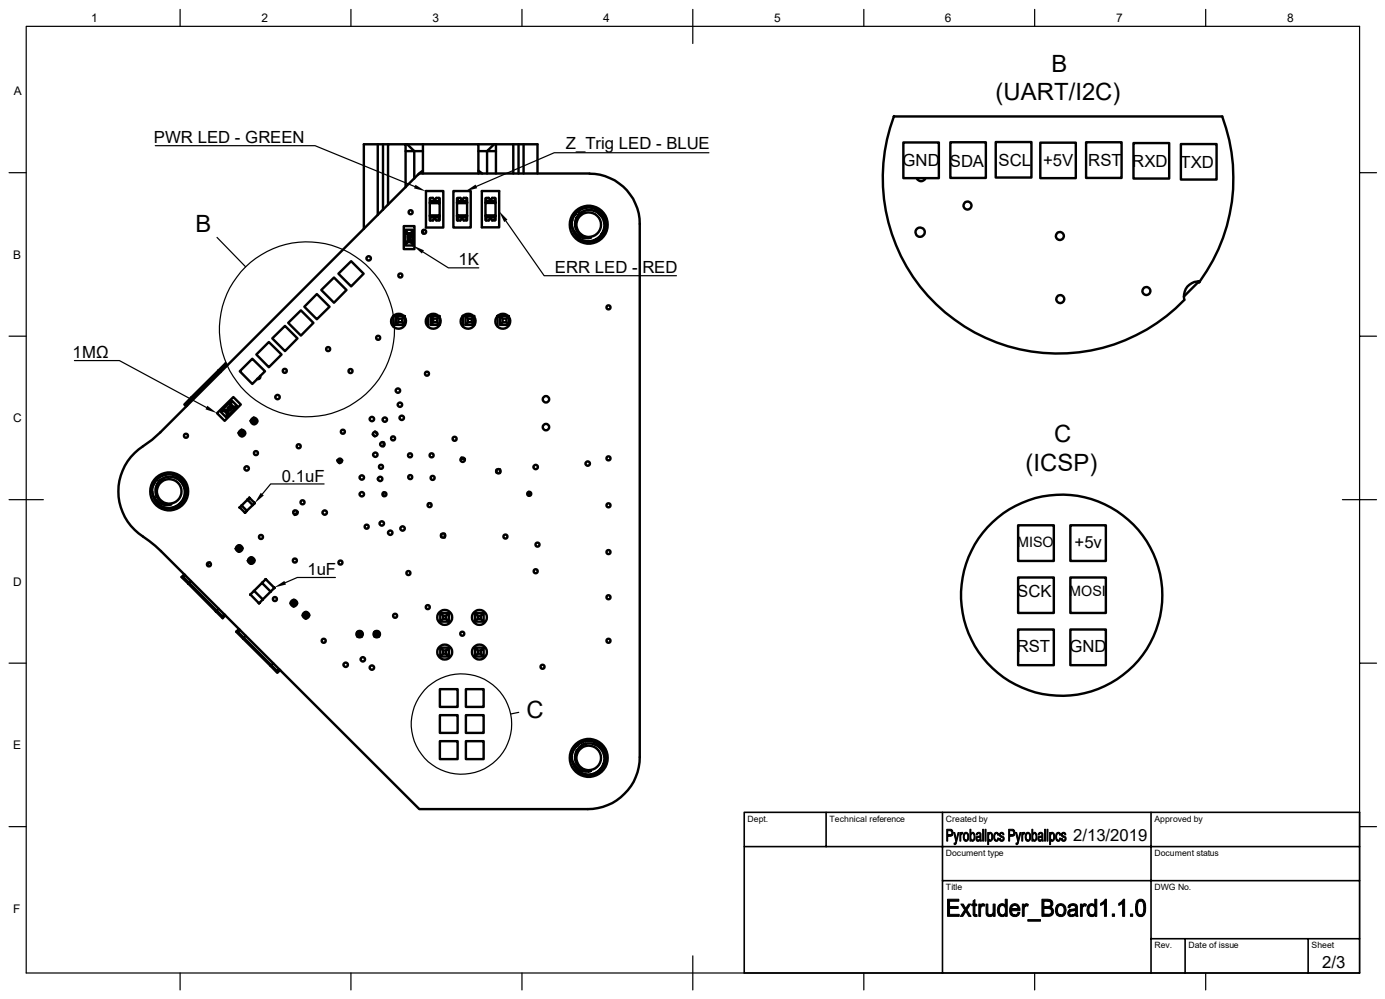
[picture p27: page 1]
Dept.; Technical reference; Created by; Approved by; Document type; Document status; Title; DWG No.; Rev.; Date of issue; Sheet; B (UART/I2C); C (ICSP); MISO; SCK MOSI; RST; GND

Z_Trig LED - BLUE PWR LED - GREEN

GND SDA SCL +5V RST RXD TXD

ERR LED - RED

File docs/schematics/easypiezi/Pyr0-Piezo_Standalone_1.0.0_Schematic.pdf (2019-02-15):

1 of 2

## LM358PWRDFN-8

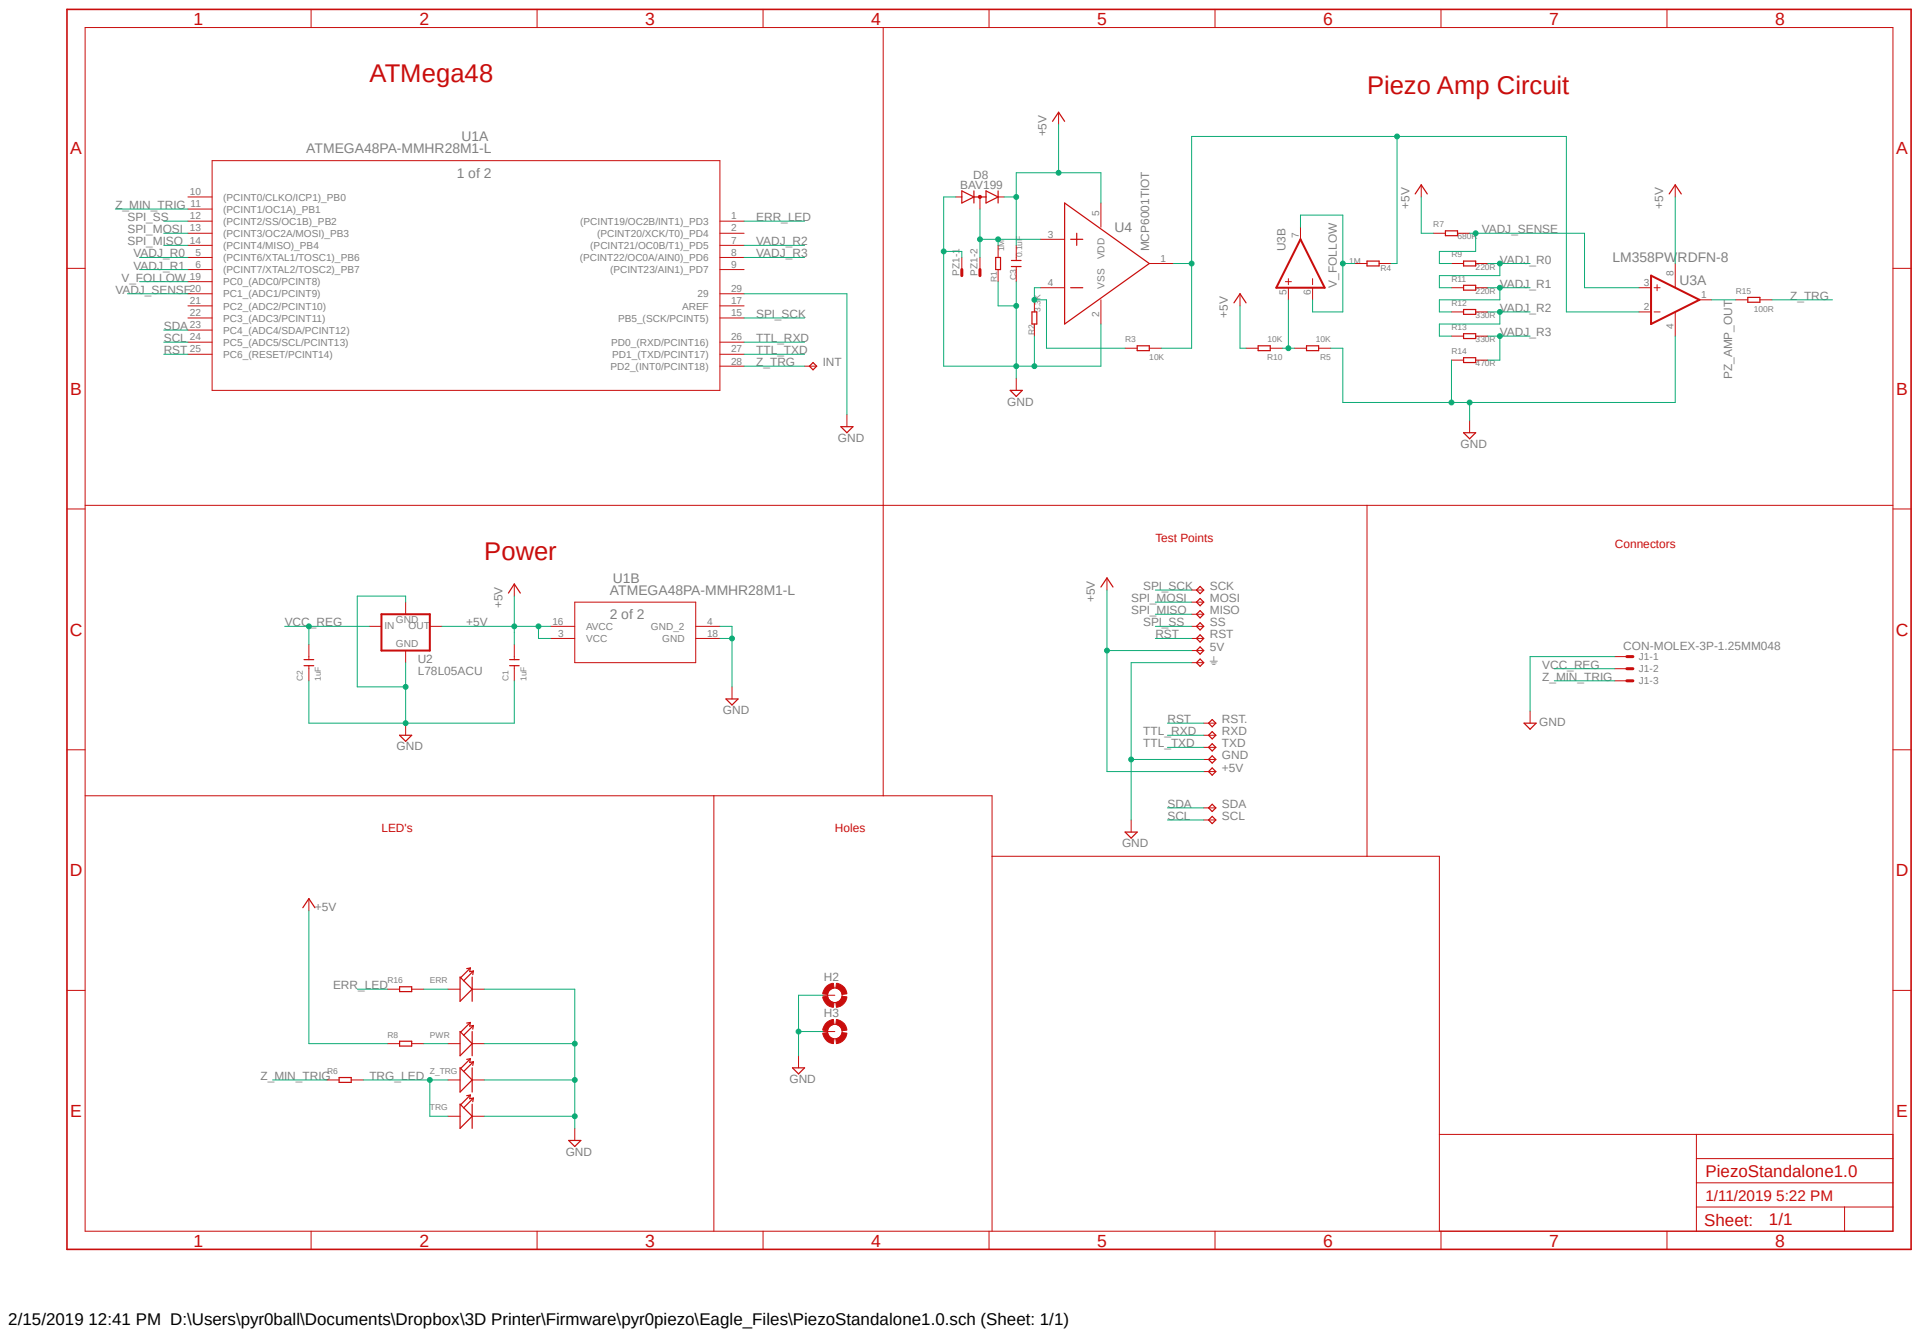
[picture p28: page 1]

ATMega48 U1A ATMEGA48PA-MMHR28M1-L | Piezo Amp Circuit

2/15/2019 12:41 PM D:\Users\pyr0ball\Documents\Dropbox\3D Printer\Firmware\pyr0piezo\Eagle_Files\PiezoStandalone1.0.sch (Sheet: 1/1)

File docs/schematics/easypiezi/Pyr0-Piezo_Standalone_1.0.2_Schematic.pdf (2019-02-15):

1 of 2

# CON-MOLEX-4P-1.25MM048 ⁺⁵V

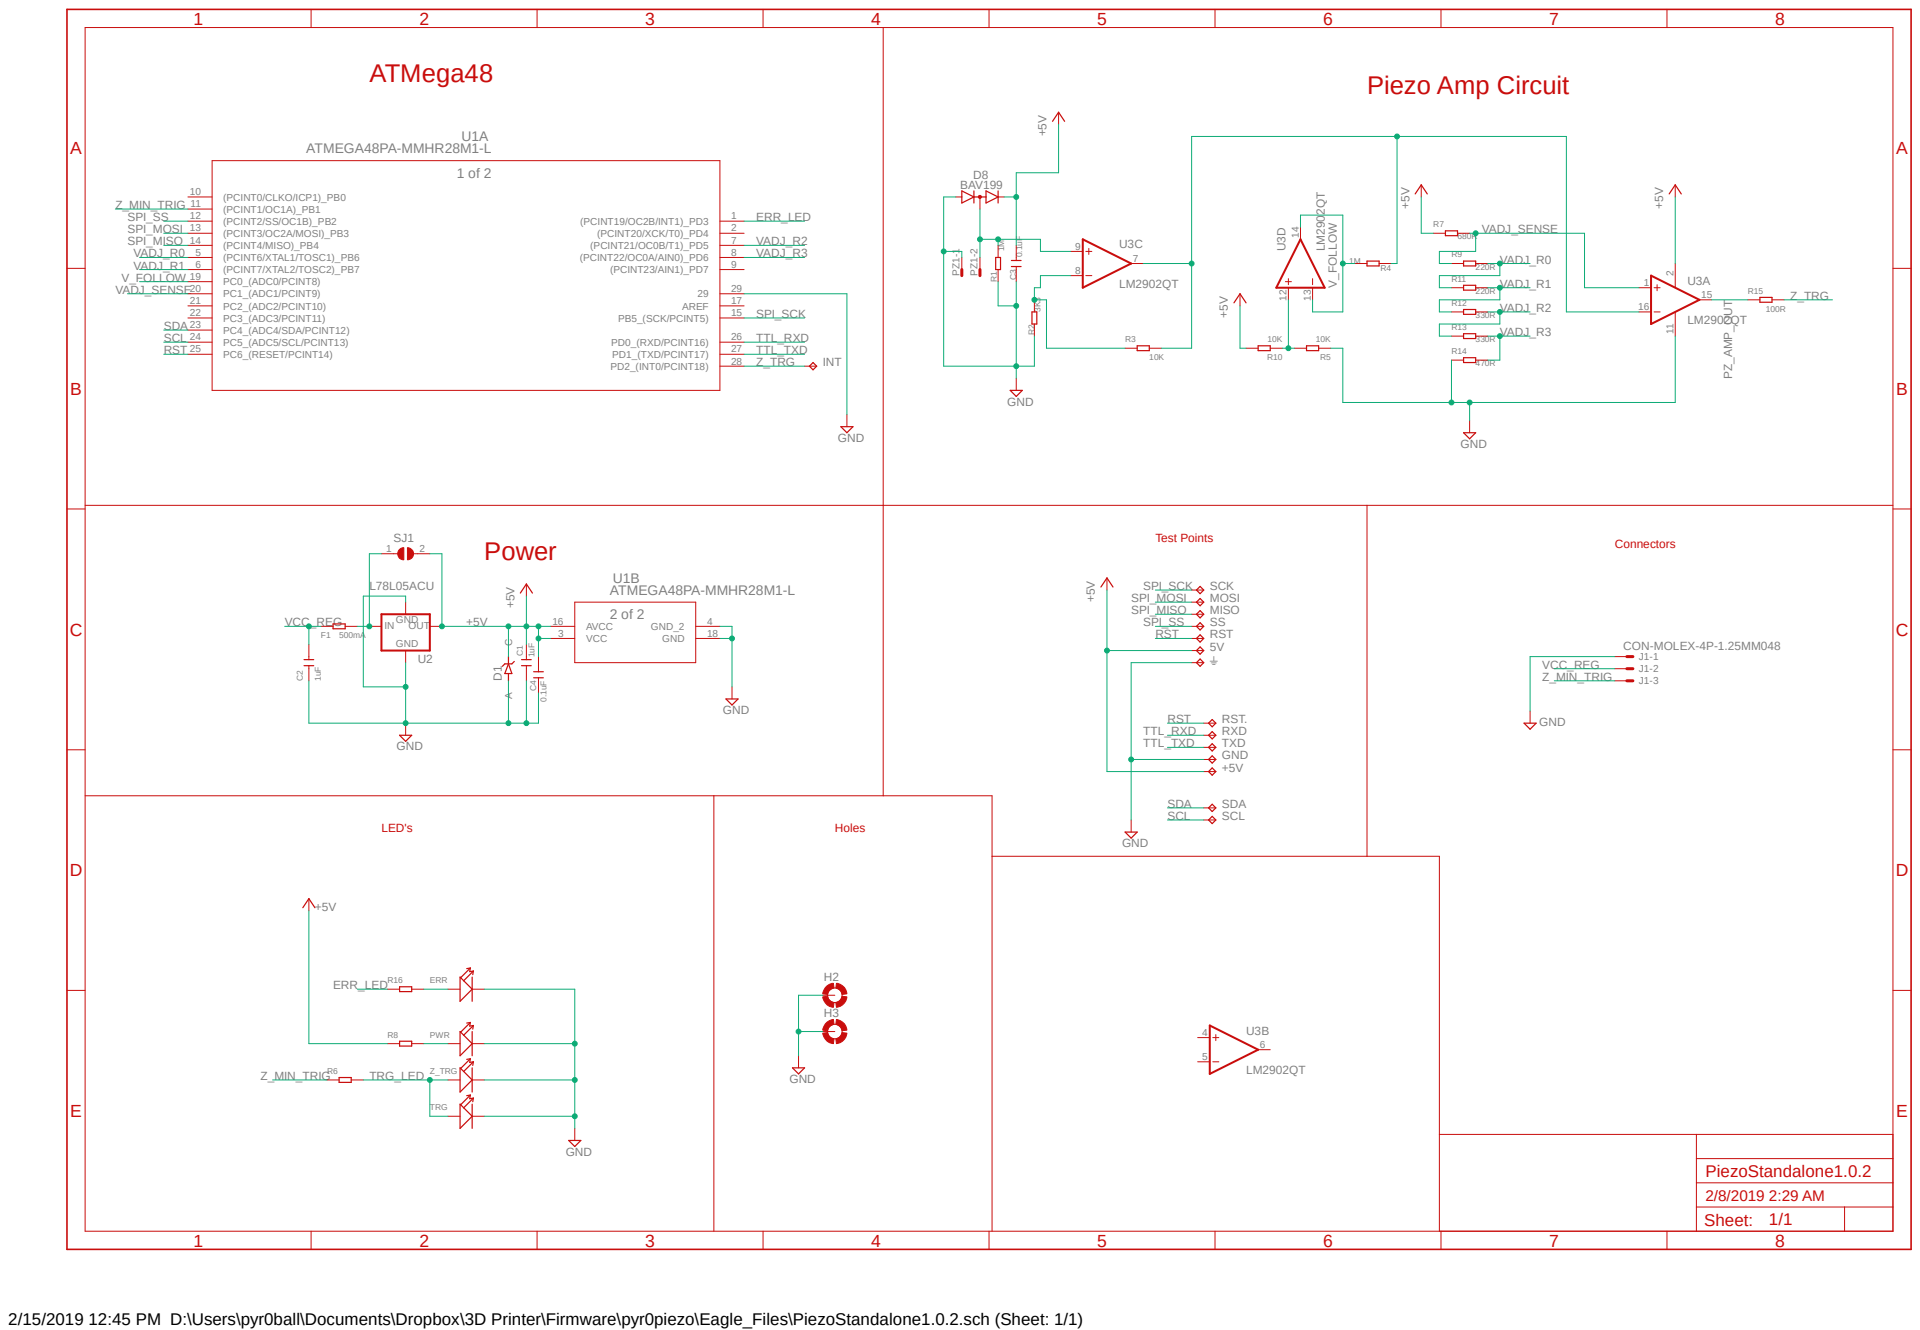
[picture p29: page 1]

ATMega48 U1A ATMEGA48PA-MMHR28M1-L | Piezo Amp Circuit

2/15/2019 12:45 PM D:\Users\pyr0ball\Documents\Dropbox\3D Printer\Firmware\pyr0piezo\Eagle_Files\PiezoStandalone1.0.2.sch (Sheet: 1/1)

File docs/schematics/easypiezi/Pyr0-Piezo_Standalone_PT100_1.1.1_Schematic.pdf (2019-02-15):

1 of 2

# CON-MOLEX-4P-1.25MM048 ⁺⁵V

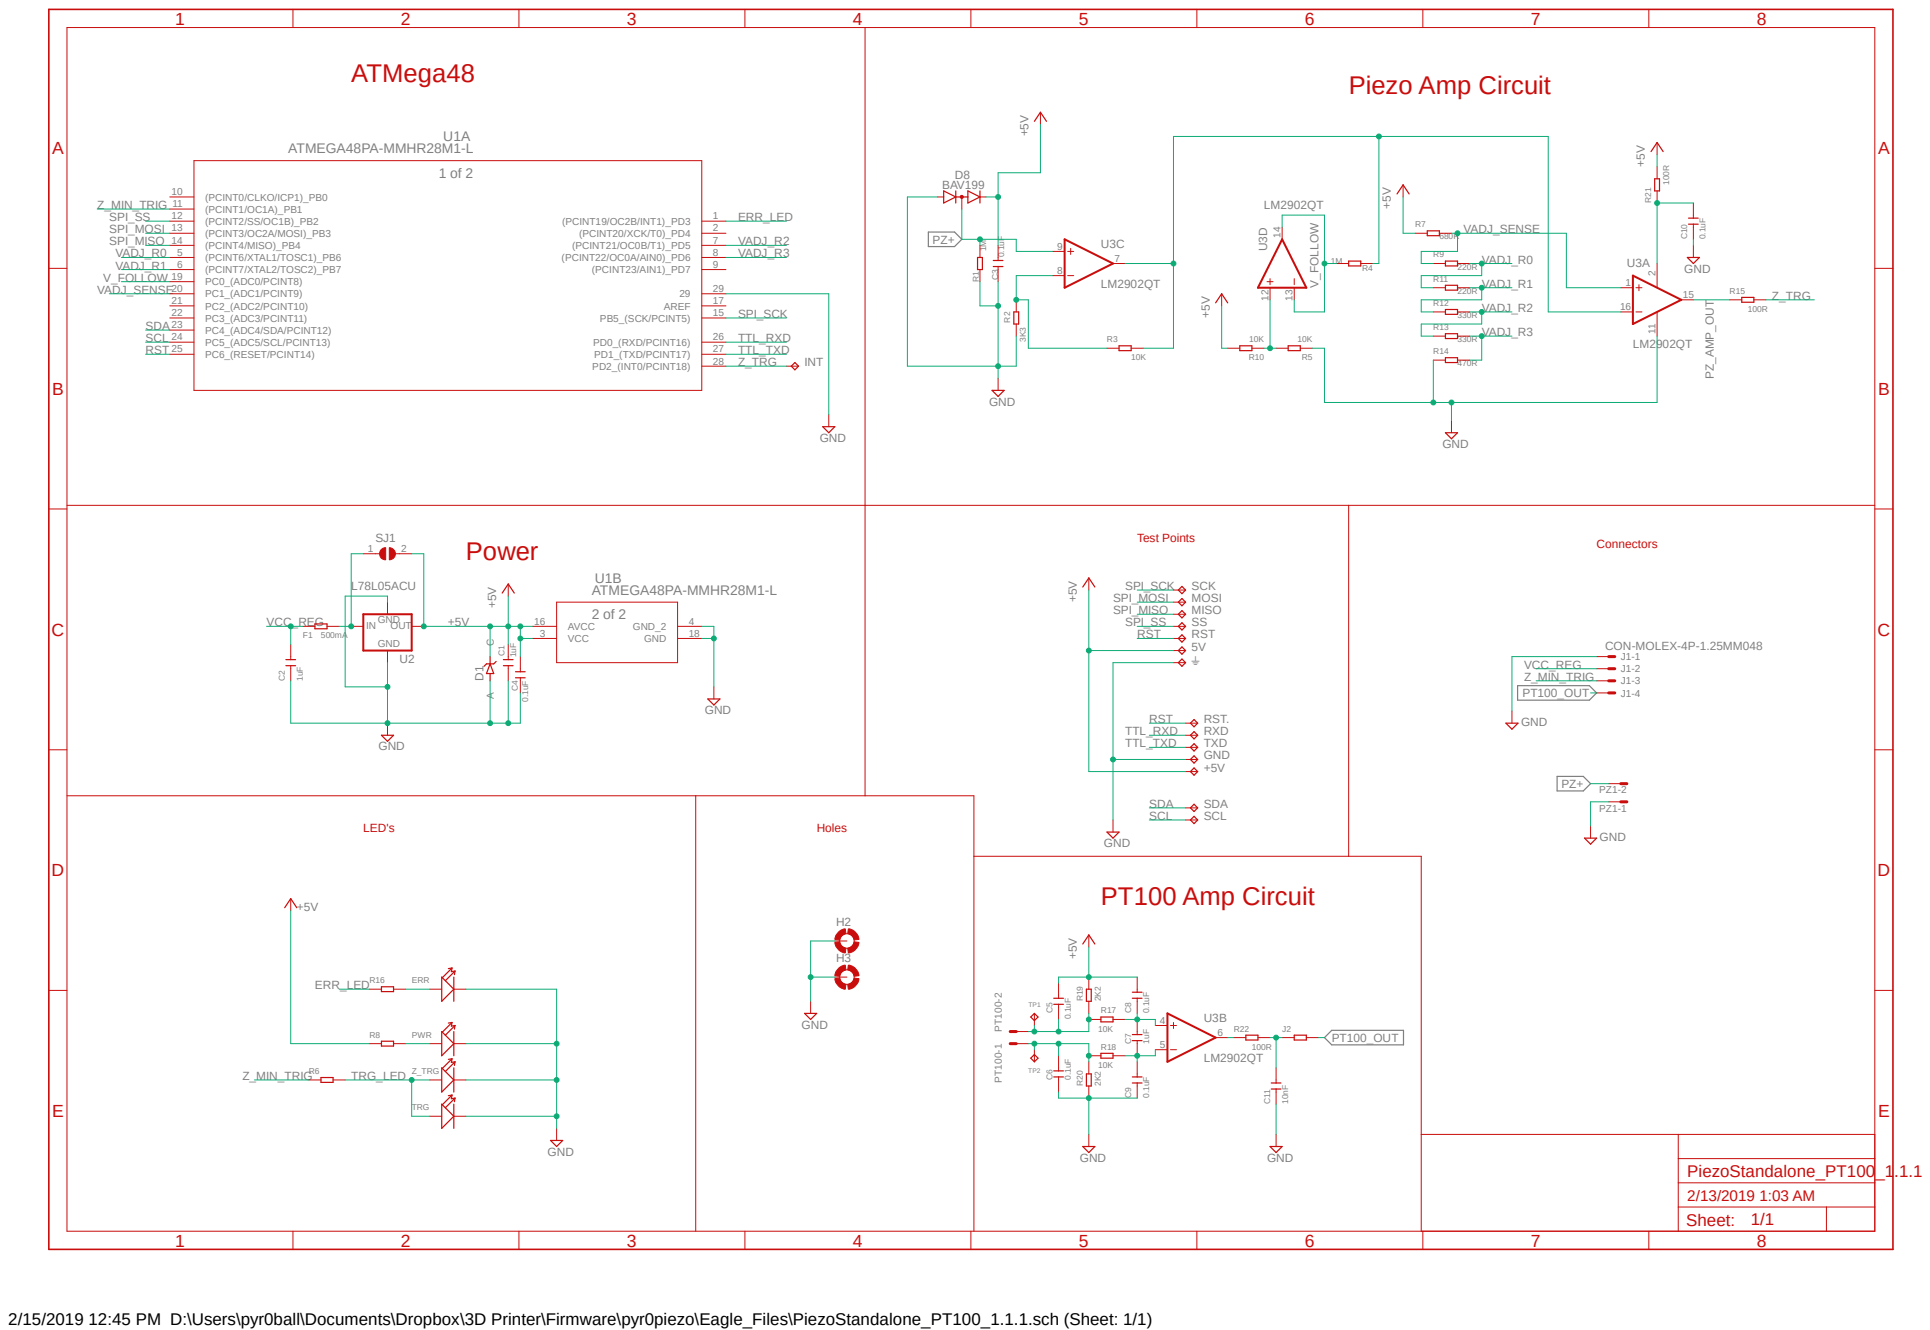
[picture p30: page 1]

ATMega48 U1A ATMEGA48PA-MMHR28M1-L | Piezo Amp Circuit

PT100 Amp Circuit

Sheet: 1/1

2/15/2019 12:45 PM D:\Users\pyr0ball\Documents\Dropbox\3D Printer\Firmware\pyr0piezo\Eagle_Files\PiezoStandalone_PT100_1.1.1.sch (Sheet: 1/1)

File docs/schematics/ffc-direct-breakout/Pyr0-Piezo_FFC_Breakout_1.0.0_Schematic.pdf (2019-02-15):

A

A

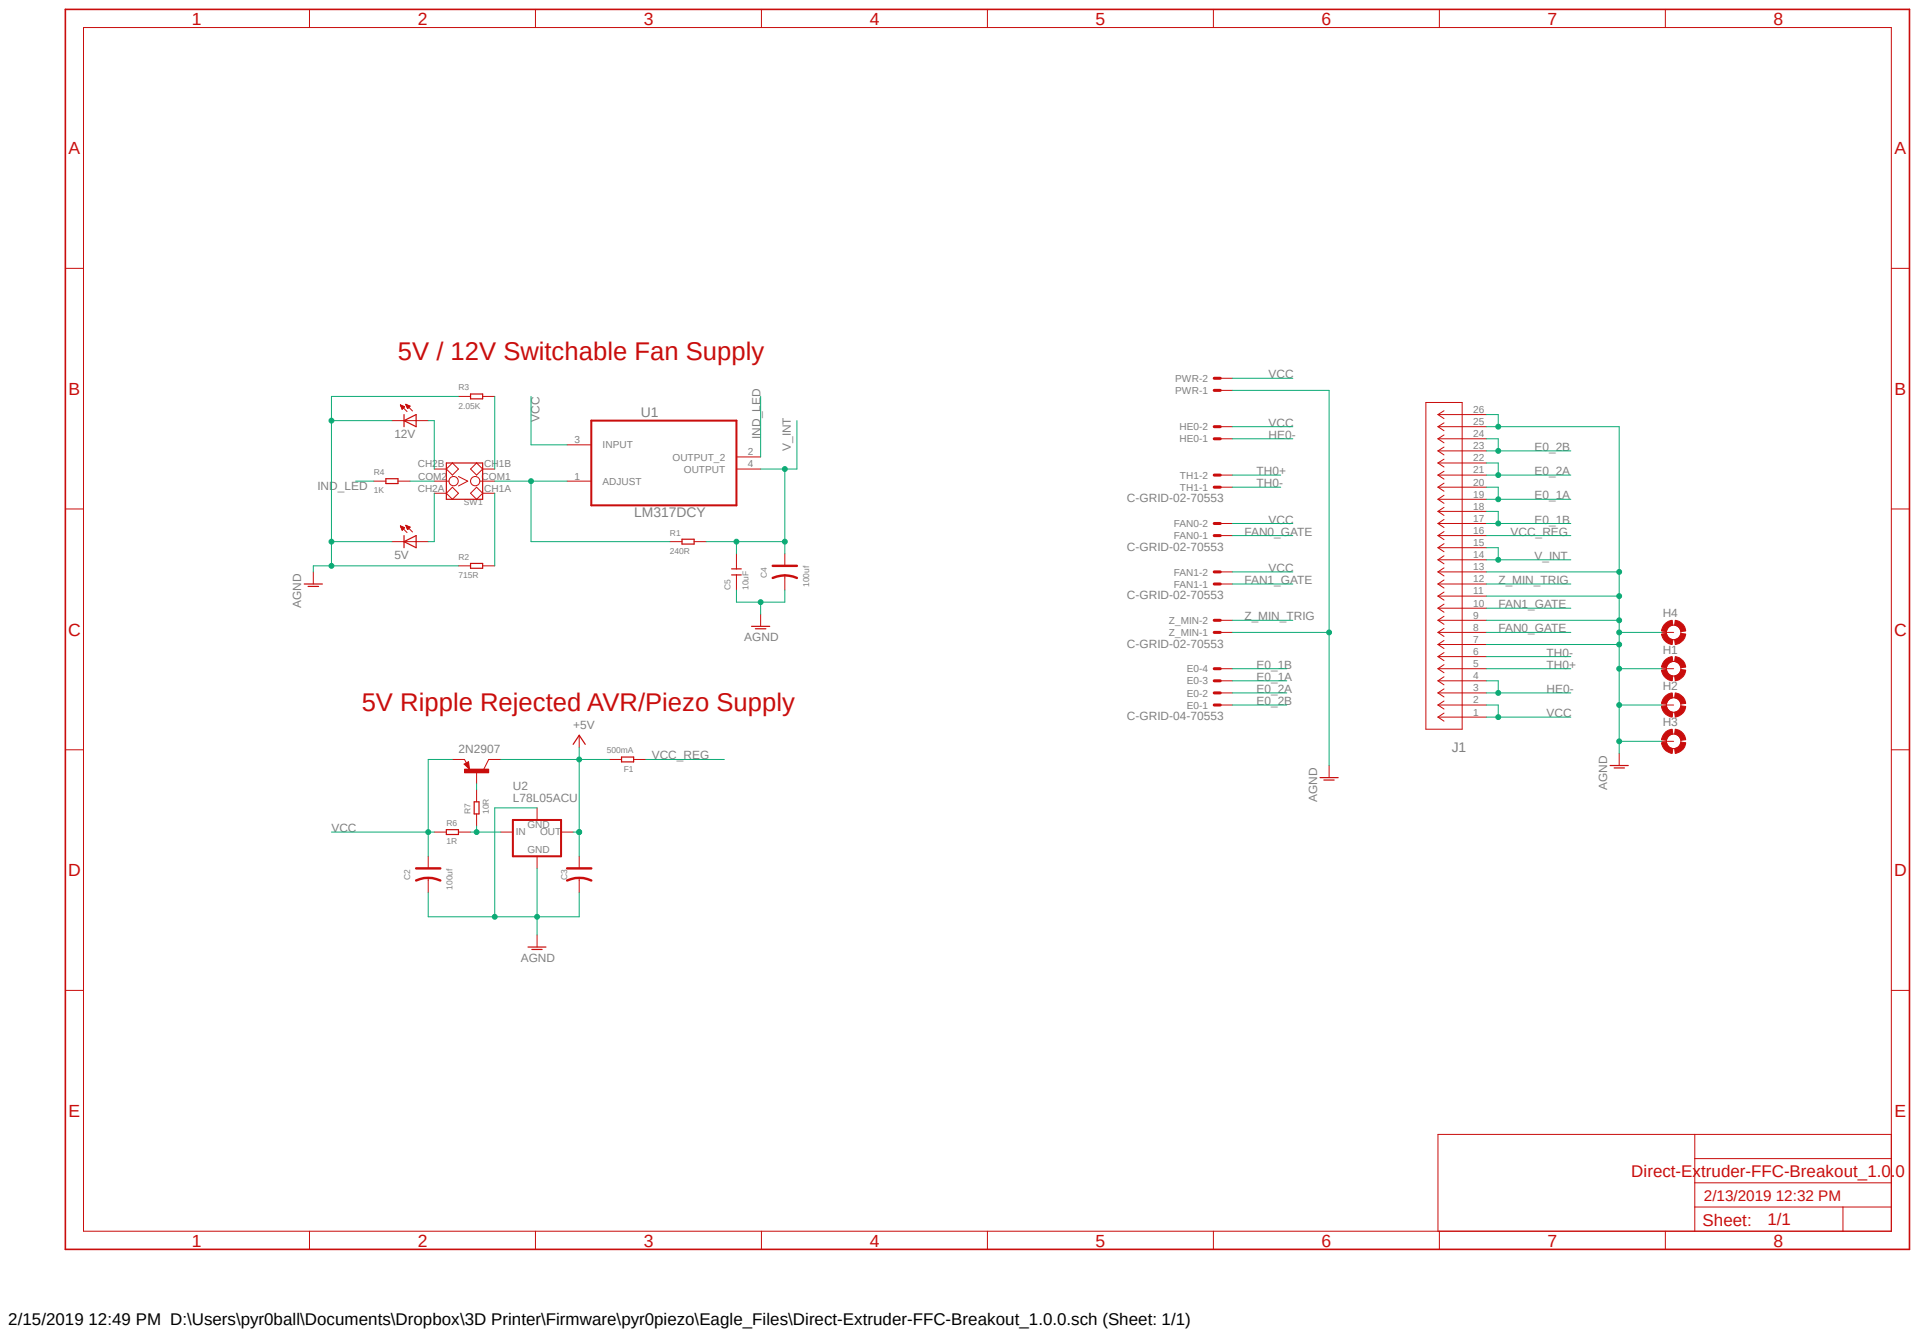
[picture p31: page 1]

5V Ripple Rejected AVR/Piezo Supply

2/15/2019 12:49 PM D:\Users\pyr0ball\Documents\Dropbox\3D Printer\Firmware\pyr0piezo\Eagle_Files\Direct-Extruder-FFC-Breakout_1.0.0.sch (Sheet: 1/1)

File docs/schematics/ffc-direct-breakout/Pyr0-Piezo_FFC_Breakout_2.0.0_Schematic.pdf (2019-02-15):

A

A

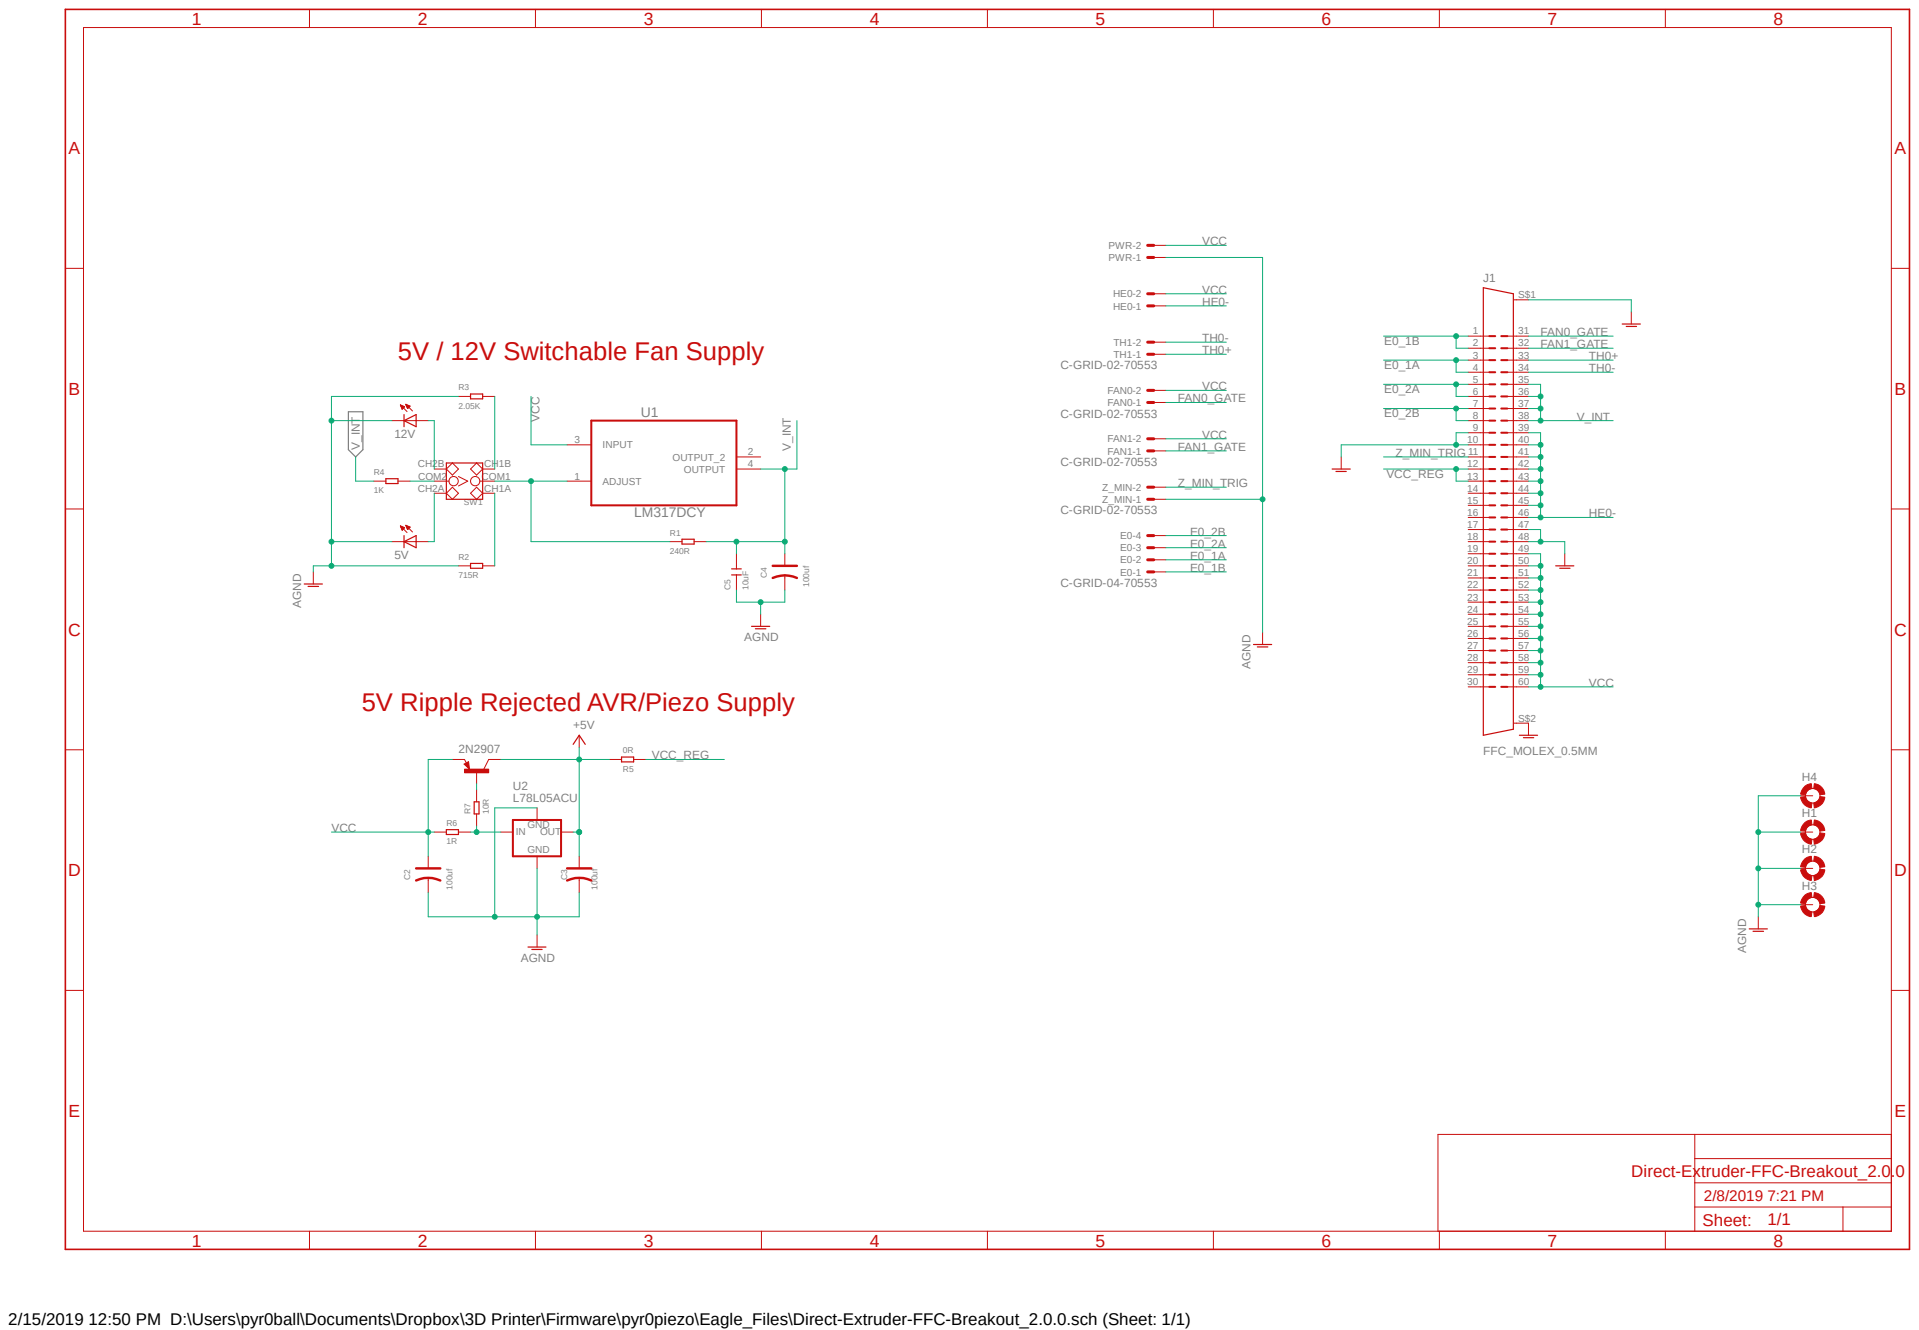
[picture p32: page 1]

5V Ripple Rejected AVR/Piezo Supply

2/15/2019 12:50 PM D:\Users\pyr0ball\Documents\Dropbox\3D Printer\Firmware\pyr0piezo\Eagle_Files\Direct-Extruder-FFC-Breakout_2.0.0.sch (Sheet: 1/1)

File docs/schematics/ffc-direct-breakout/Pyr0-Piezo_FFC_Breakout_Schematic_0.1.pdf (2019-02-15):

A

A

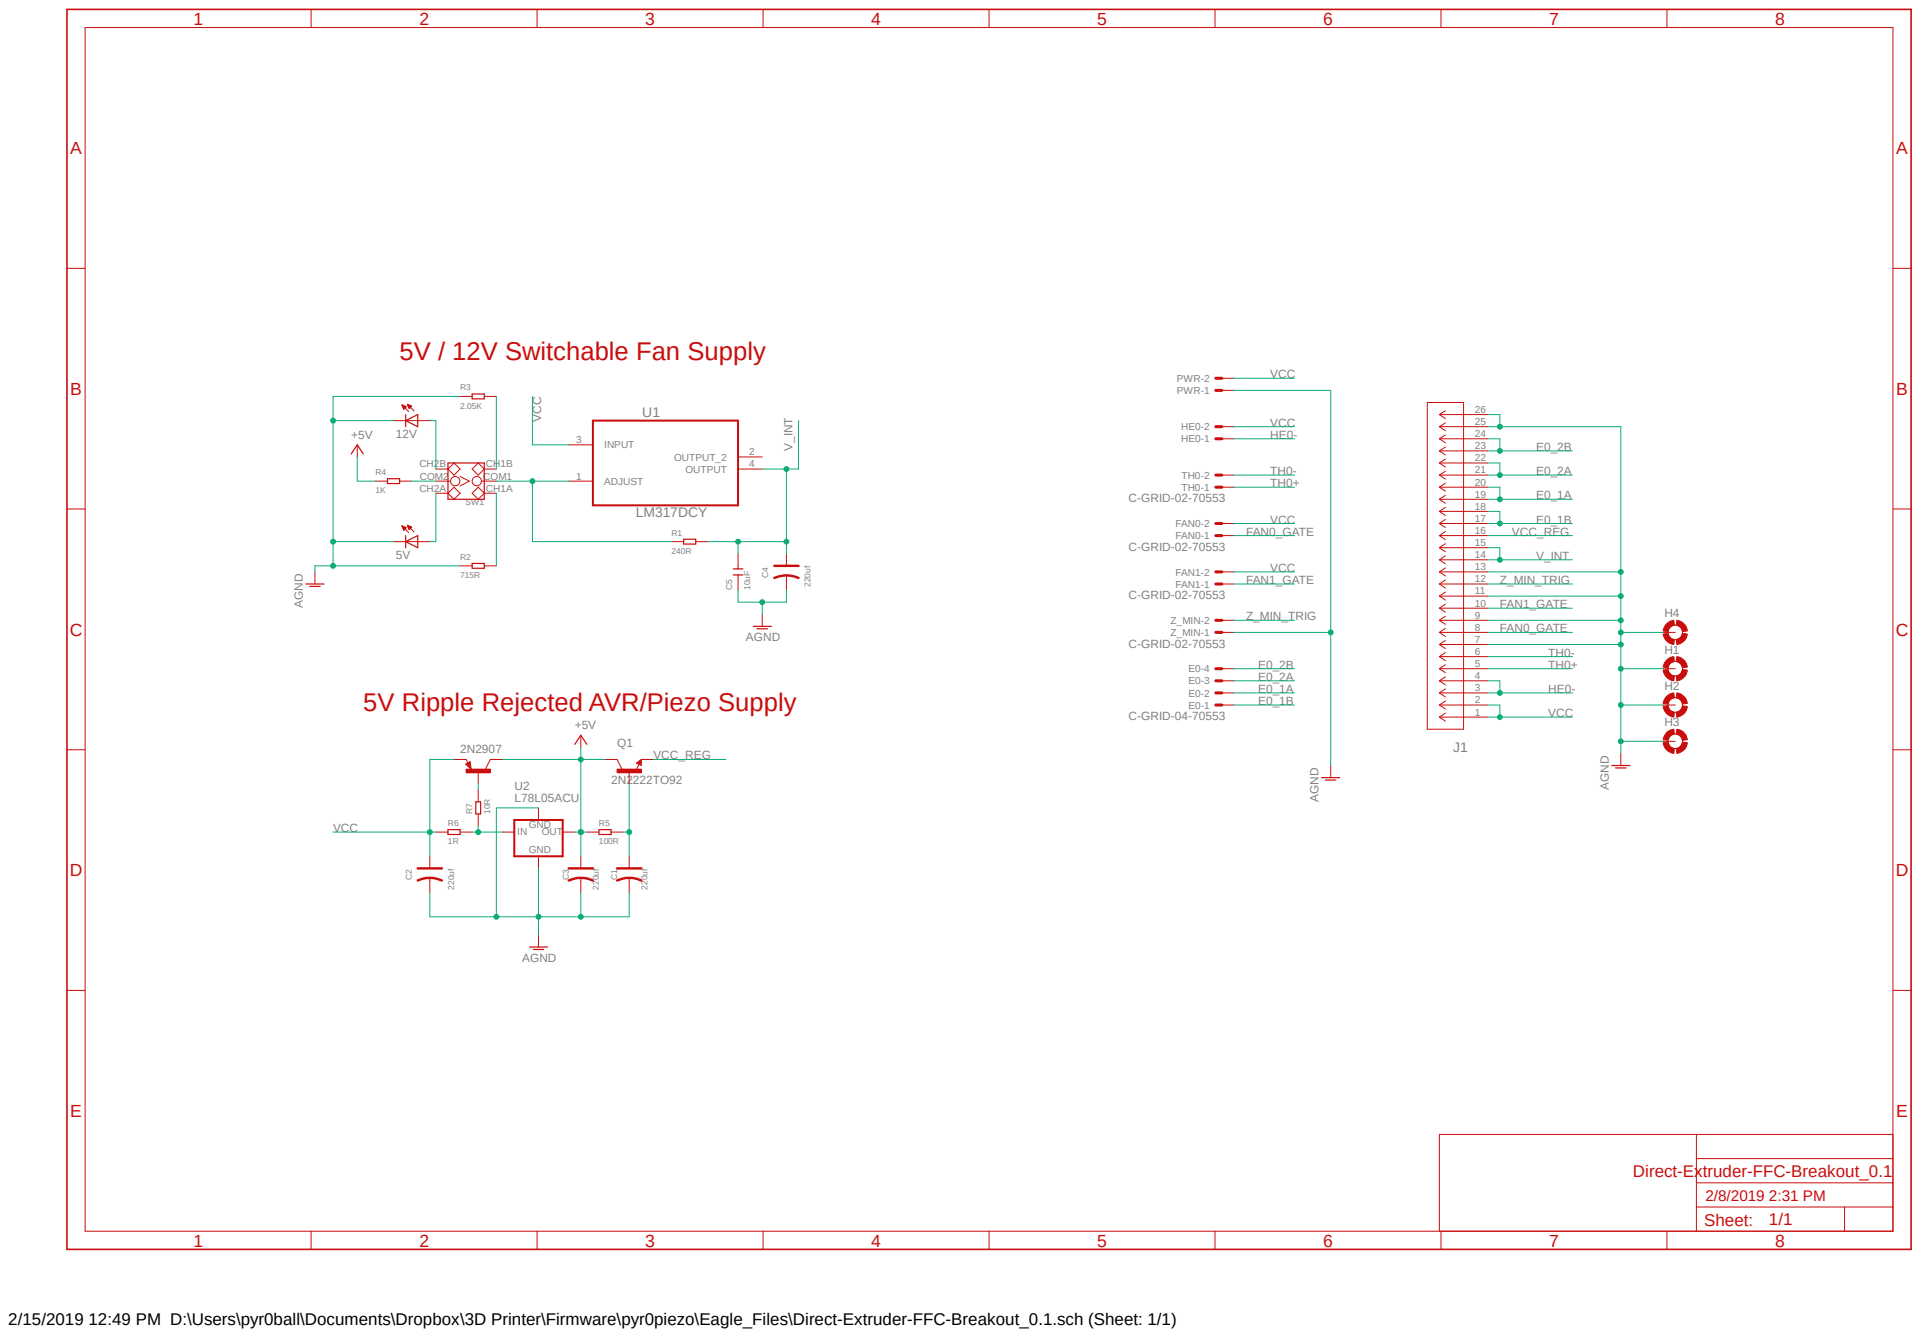
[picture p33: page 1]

5V Ripple Rejected AVR/Piezo Supply

2/15/2019 12:49 PM D:\Users\pyr0ball\Documents\Dropbox\3D Printer\Firmware\pyr0piezo\Eagle_Files\Direct-Extruder-FFC-Breakout_0.1.sch (Sheet: 1/1)

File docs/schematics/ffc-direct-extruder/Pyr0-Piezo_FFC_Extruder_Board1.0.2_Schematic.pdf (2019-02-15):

1 of 2

## LM358PWRDFN-8

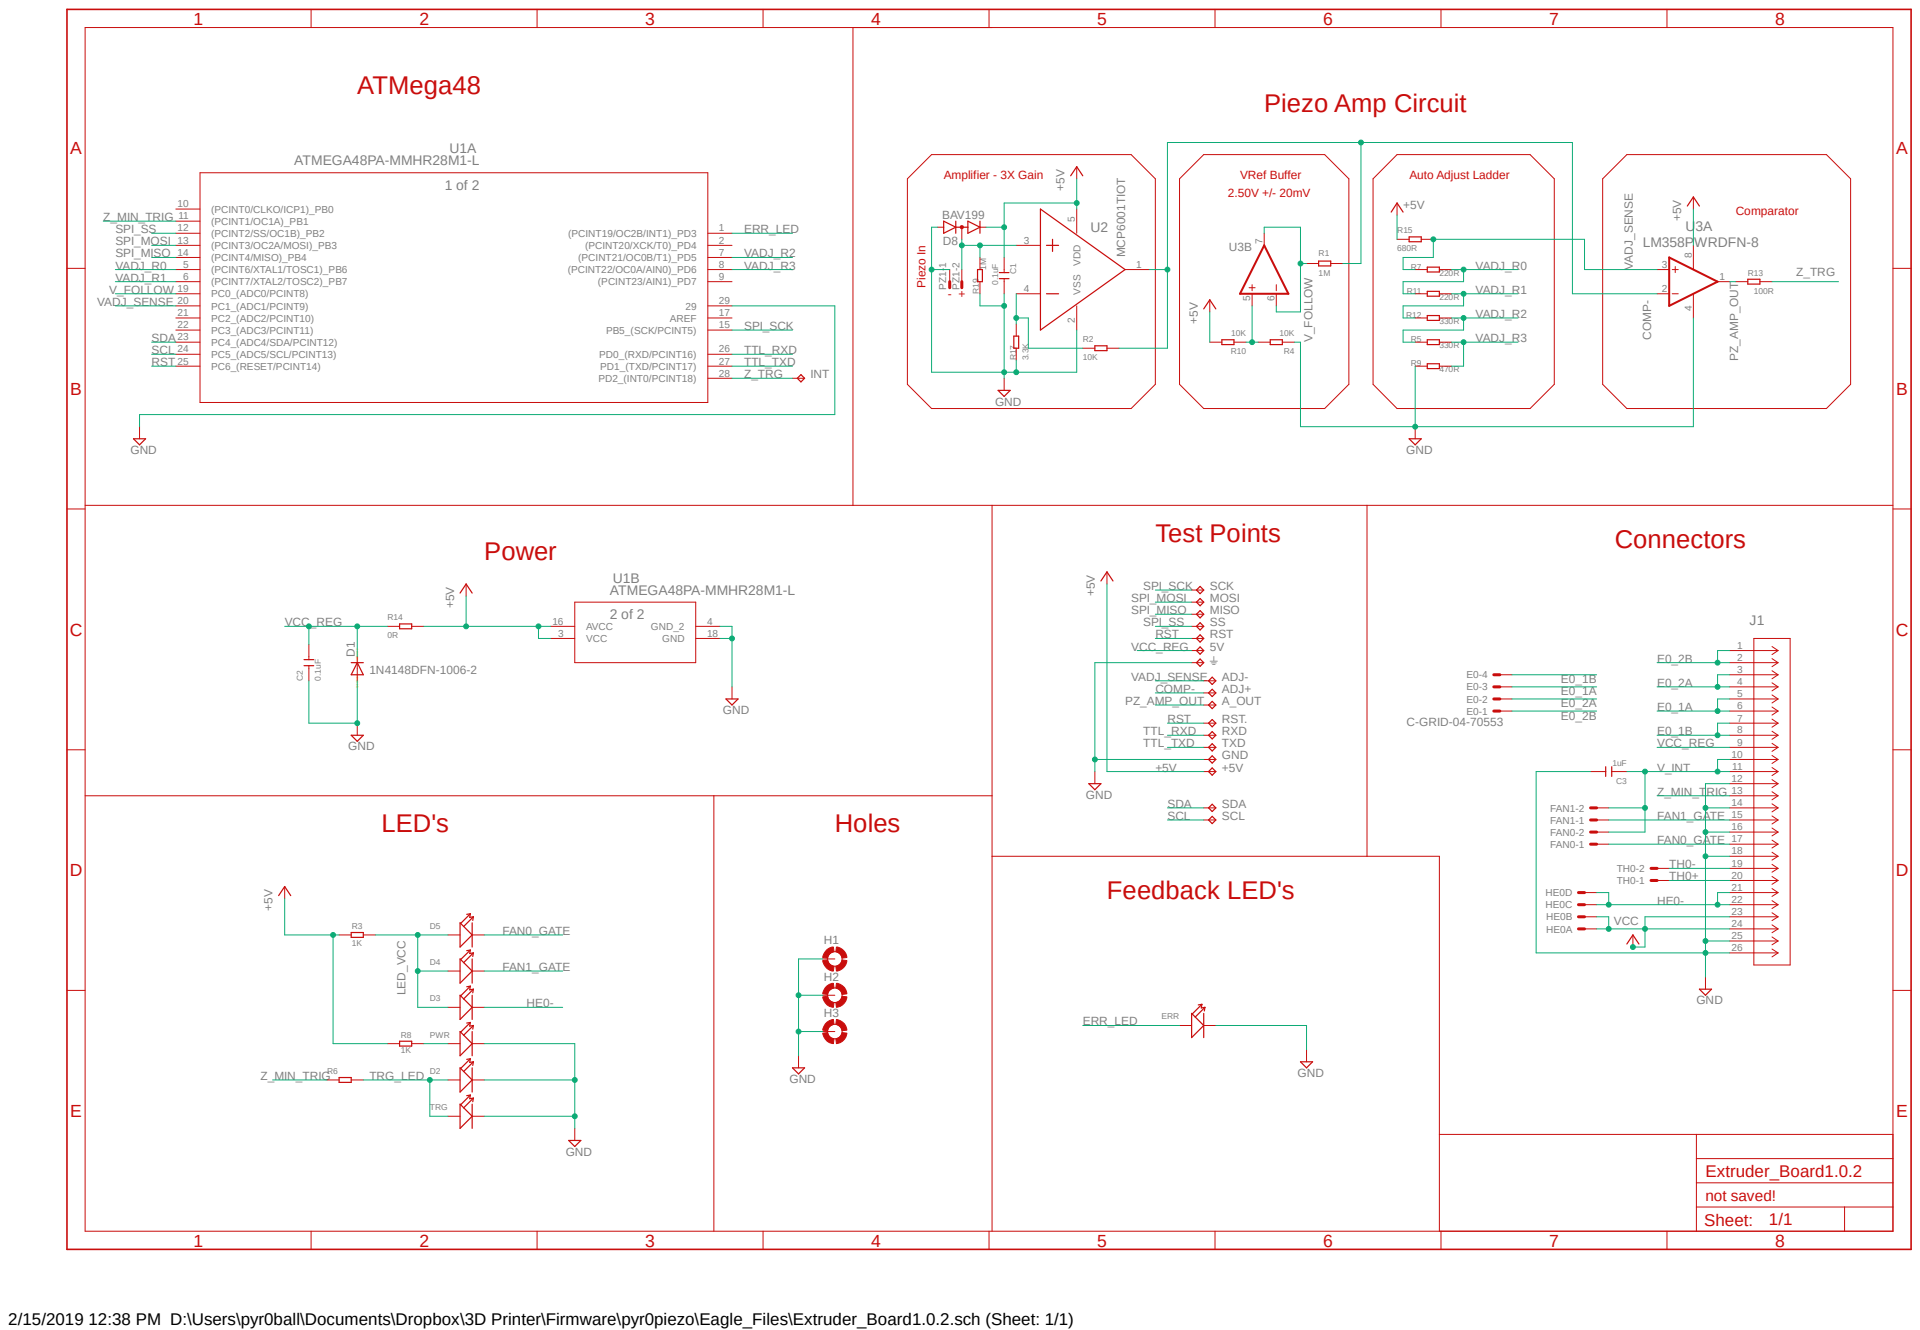
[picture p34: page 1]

ATMega48 U1A ATMEGA48PA-MMHR28M1-L | Piezo Amp Circuit

2/15/2019 12:38 PM D:\Users\pyr0ball\Documents\Dropbox\3D Printer\Firmware\pyr0piezo\Eagle_Files\Extruder_Board1.0.2.sch (Sheet: 1/1) SpiceOrder 1 SpiceOrder 2

Feedback LED's GND

Sheet: 1/1

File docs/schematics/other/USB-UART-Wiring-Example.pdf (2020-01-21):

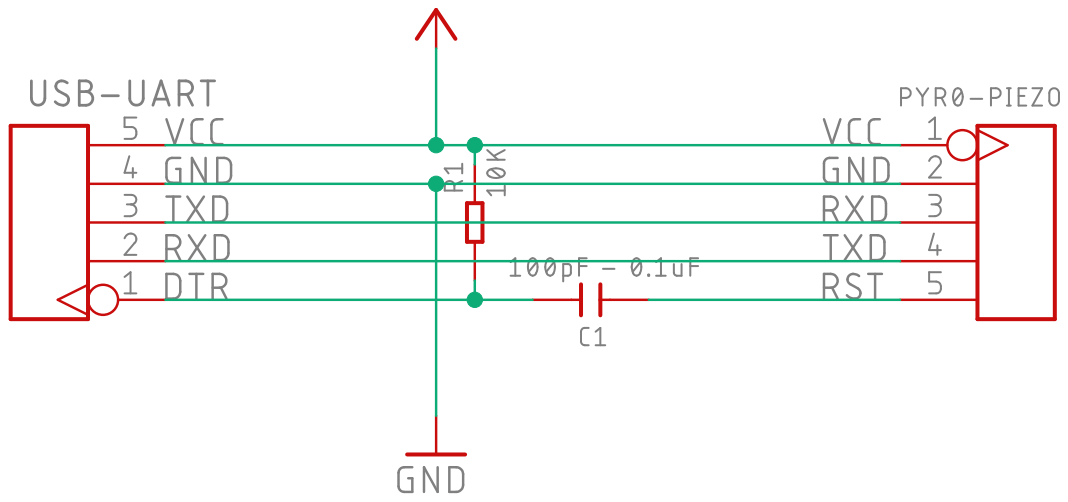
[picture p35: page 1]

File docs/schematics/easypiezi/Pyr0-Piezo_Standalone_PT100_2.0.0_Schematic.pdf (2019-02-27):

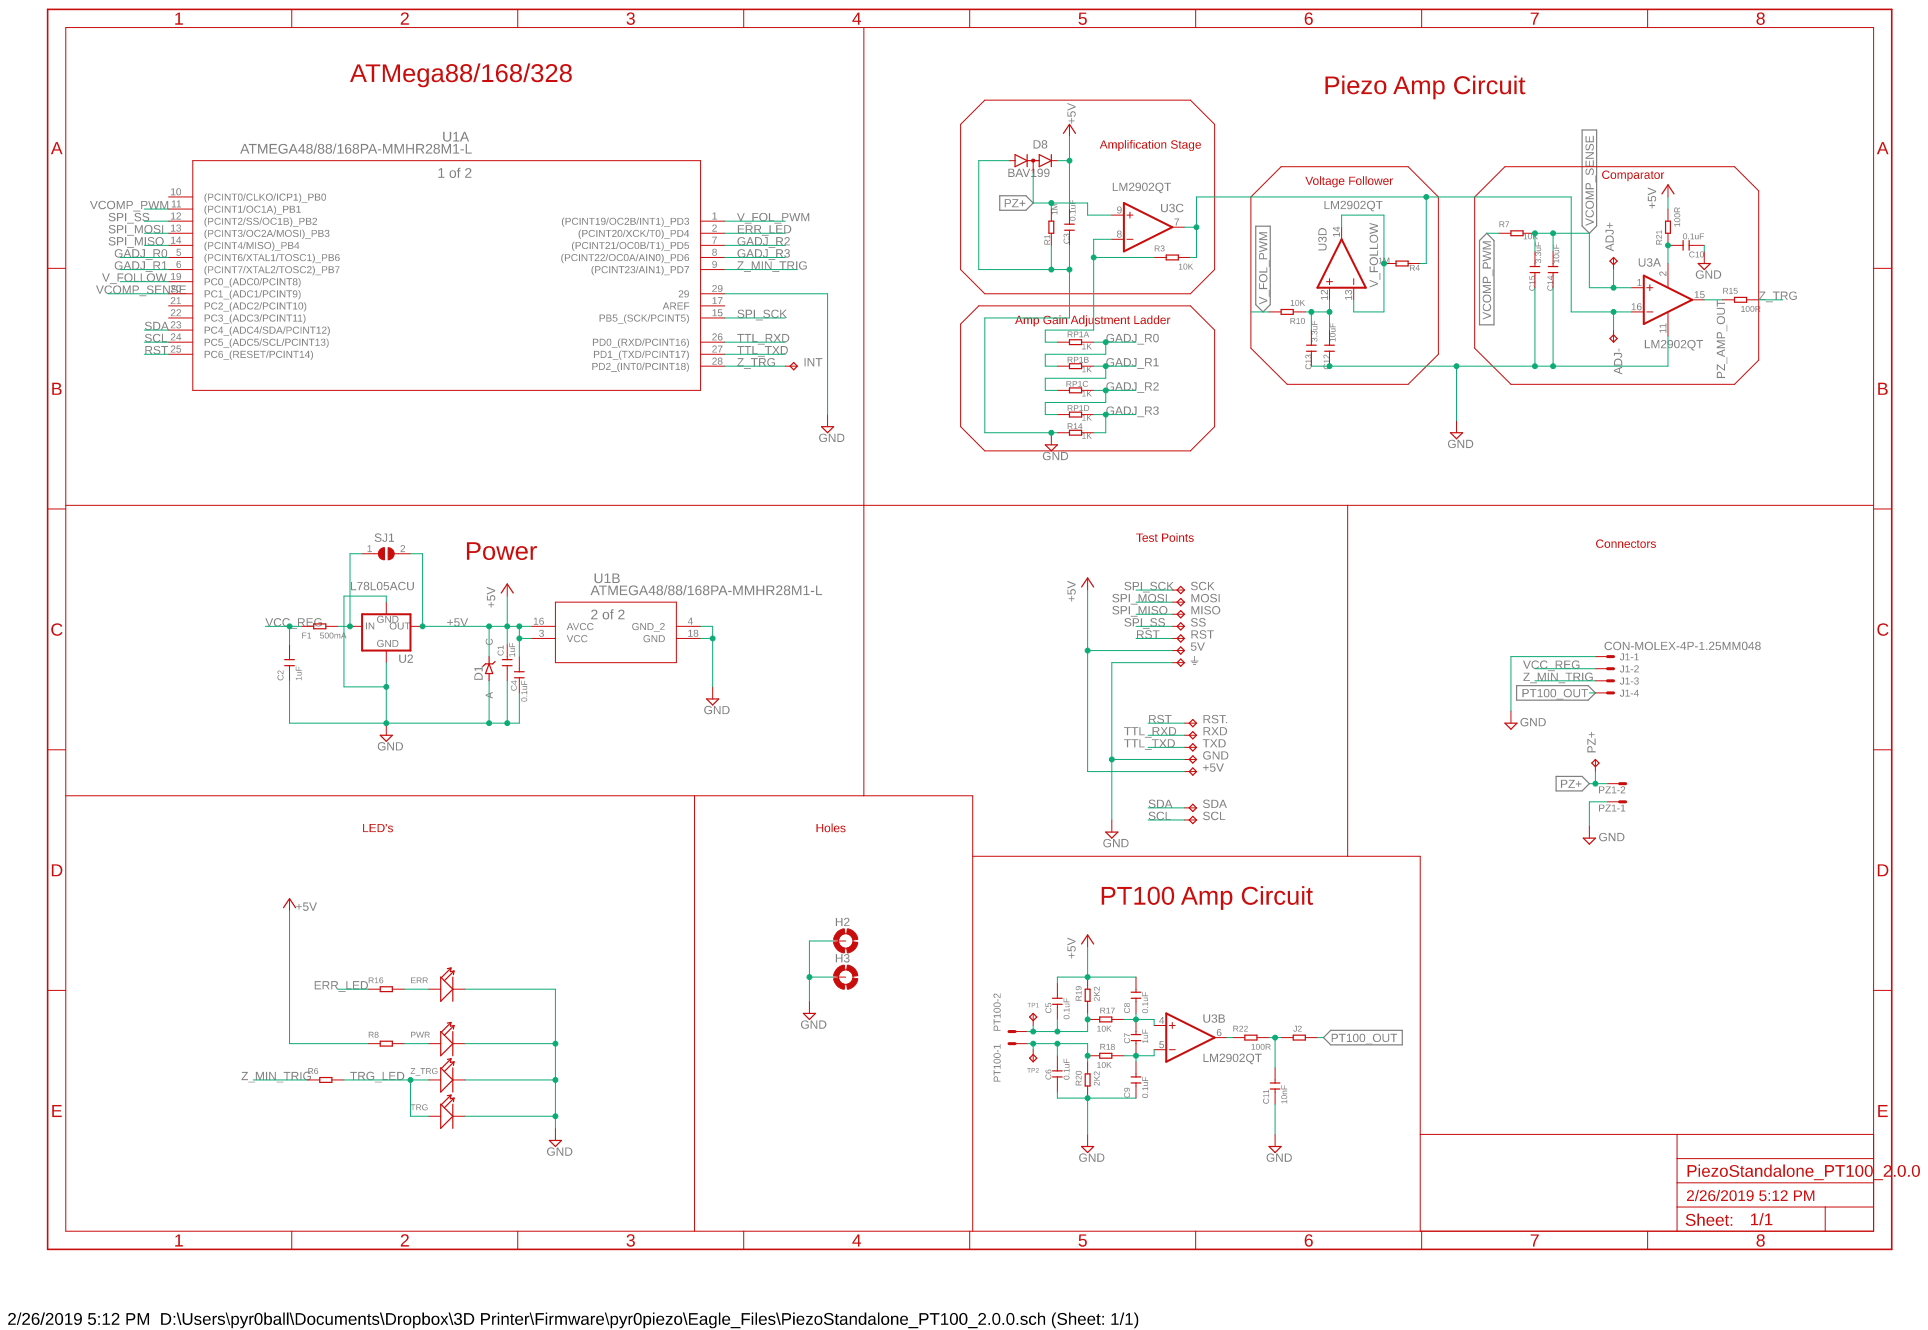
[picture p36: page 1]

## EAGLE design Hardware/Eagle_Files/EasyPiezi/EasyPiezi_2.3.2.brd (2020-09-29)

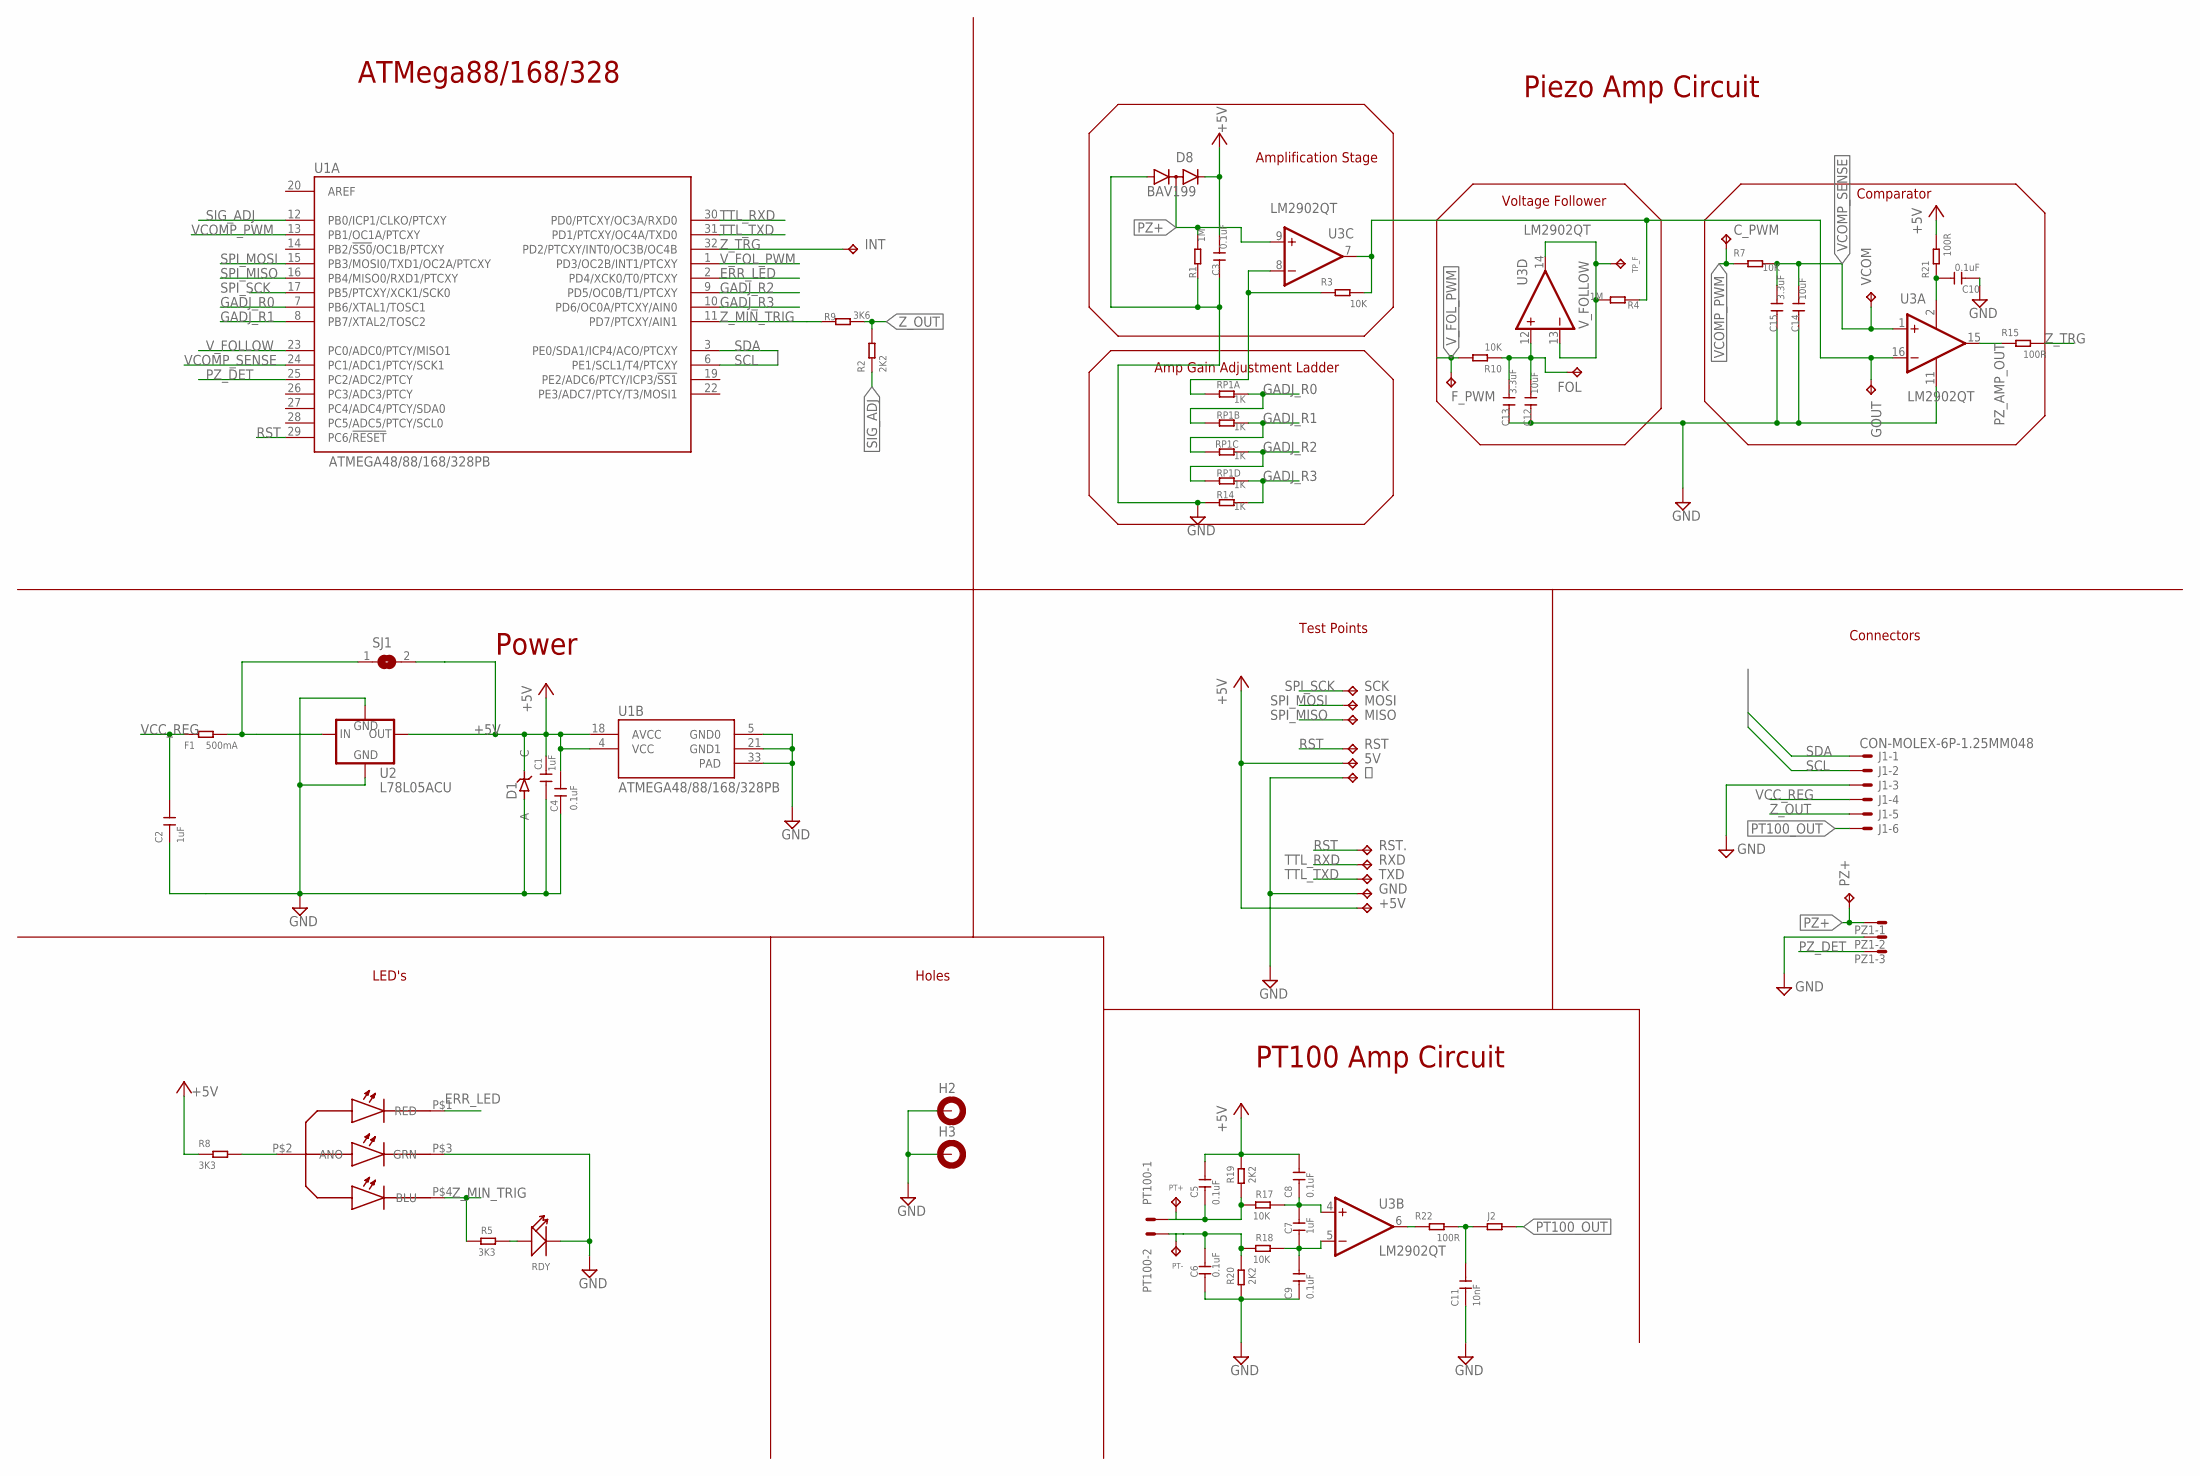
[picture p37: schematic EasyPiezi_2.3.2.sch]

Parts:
5V: TPTP13SQ; TP13SQ
+5V: TPTP13SQ; TP13SQ
C1, C2: 1uF; CAPC1609X80
C3, C4, C5, C6, C8, C9, C10: 0.1uF; CAPC1005X50
C7: 1uF; CAPC1005X50
C11: 10nF; CAPC1005X50
C12, C14: 10uF; CAPC1005X50
C13, C15: 3.3uF; CAPC1005X50
C_PWM: TPTP06R; TP06R
D1: DIODE_ZENER_PLZ5V1C; DO-219AC
D8: BAV199; SOT23
F1: 500mA; R0402
FOL: TPTP13SQ; TP13SQ
F_PWM: TPTP09R; TP09R
GND: TPTP13SQ; TP13SQ
GOUT: TPTP13SQ; TP13SQ
H2, H3: HOLES_MOUNT-PAD-ROUND3.2; HOLES_3,2-PAD
INT: TPTP06R; TP06R
J1: CON-MOLEX-6P-1.25MM048; 53048-06
J2: SEEED-RESISTOR_SMD-RES-1.5K-1%-1/10W(0603)DETAILE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; SEEED-RESISTOR_R0603
LED: LED-RGB-COM_ANO0606; 0606_LED
MISO: TPTP13SQ; TP13SQ
MOSI: TPTP13SQ; TP13SQ
PT100: CON-MOLEX-2P-1.27MM048; 53048-02
PT+: TPTP09R; TP09R
PT-: TPTP09R; TP09R
PZ1: CON-MOLEX-3P-1.25MM048; 53048-03
PZ+: TPTP13SQ; TP13SQ
R1, R4: 1M; R0402
R2, R19, R20: 2K2; R0402
R3, R7, R10, R17, R18: 10K; R0402
R5, R8: 3K3; R0402
R9: 3K6; R0402
R14: 1K; R0402
R15, R21, R22: 100R; R0402
RDY: SEEED-LED_SMD-LED-CLEAR-BLUE(0603)LED_0603; SEEED-LED_LED-0603
RP1: 1K; EXBN8V-L
RST, RST.: TPTP13SQ; TP13SQ
RXD: TPTP13SQ; TP13SQ
SCK: TPTP13SQ; TP13SQ
SJ1: SJ
TP_F: TPTP09R; TP09R
TXD: TPTP13SQ; TP13SQ
U1: ATMEGA48/88/168/328PB; QFN50P500X500X90-33N
U2: L78L05ACU; SOT89
U3: LM2902QT; QFN16
VCOM: TPTP13SQ; TP13SQ
⏚: TPTP13SQ; TP13SQ

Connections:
+5V: 5V.TP, +5V.TP, C1.2, C3.2, C4.2, C5.2, C8.2, D1.P$2 (C), D8.2 (C), R8.1, R19.2, R21.2, SJ1.2, U1.4 (VCC), U1.18 (AVCC), U2.1 (OUT)
AMP_VCC: C10.2, R21.1, U3.2 (V+)
ERR_LED: LED.P$1 (RED), U1.2 (PD4/XCK0/T0/PTCXY)
GADJ_R0: RP1.2 (1), RP1.8 (2), U1.7 (PB6/XTAL1/TOSC1)
GADJ_R1: RP1.3 (1), RP1.7 (2), U1.8 (PB7/XTAL2/TOSC2)
GADJ_R2: RP1.4 (1), RP1.6 (2), U1.9 (PD5/OC0B/T1/PTCXY)
GADJ_R3: R14.2, RP1.5 (2), U1.10 (PD6/OC0A/PTCXY/AIN0)
GAIN_ADJ: R3.1, RP1.1, U3.8 (-IN)
GAIN_OUT: GOUT.TP, R3.2, R4.1, U3.7 (OUT), U3.16 (-IN)
GND: C1.1, C2.1, C3.1, C4.1, C6.1, C9.1, C10.1, C11.1, C12.1, C13.1, C14.1, C15.1, D1.P$1 (A), D8.1 (A), GND.TP, H2.B3,2, H3.B3,2, J1.3, LED.P$3 (GRN), PZ1.2, R1.1, R14.1, R20.1, RDY.-, U1.5 (GND0), U1.21 (GND1), U1.33 (PAD), U2.2 (GND), U2.PAD, U3.11 (V-), ⏚.TP
LED_PWR: LED.P$2 (ANO), R8.2
PT100_JUMP: C11.2, J2.1, R22.2
PT100_OUT: J1.6, J2.2
PT_AMP: R22.1, U3.6 (OUT)
PT_AMP+: C7.2, C8.1, R17.2, U3.4 (+IN)
PT_AMP-: C7.1, C9.2, R18.2, U3.5 (-IN)
PT_IN+: C5.1, PT100.1, PT+.TP, R17.1, R19.1
PT_IN-: C6.2, PT100.2, PT-.TP, R18.1, R20.2
PZ+: D8.3 (AC), PZ1.1, PZ+.TP, R1.2, U3.9 (+IN)
PZ_AMP_OUT: R15.1, U3.15 (OUT)
PZ_DET: PZ1.3, U1.25 (PC2/ADC2/PTCY)
RDY_LED: R5.2, RDY.+
RST: RST.TP, RST..TP, U1.29 (PC6/!RESET!)
SCL: J1.2, U1.6 (PE1/SCL1/T4/PTCXY)
SDA: J1.1, U1.3 (PE0/SDA1/ICP4/ACO/PTCXY)
SIG_ADJ: R2.1, U1.12 (PB0/ICP1/CLKO/PTCXY)
SPI_MISO: MISO.TP, U1.16 (PB4/MISO0/RXD1/PTCXY)
SPI_MOSI: MOSI.TP, U1.15 (PB3/MOSI0/TXD1/OC2A/PTCXY)
SPI_SCK: SCK.TP, U1.17 (PB5/PTCXY/XCK1/SCK0)
TTL_RXD: RXD.TP, U1.30 (PD0/PTCXY/OC3A/RXD0)
TTL_TXD: TXD.TP, U1.31 (PD1/PTCXY/OC4A/TXD0)
VCC_FUSE: F1.2, SJ1.1, U2.3 (IN)
VCC_REG: C2.2, F1.1, J1.4
VCOMP_PWM: C_PWM.TP, R7.1, U1.13 (PB1/OC1A/PTCXY)
VCOMP_SENSE: C14.2, C15.2, R7.2, U1.24 (PC1/ADC1/PTCY/SCK1), U3.1 (+IN), VCOM.TP
V_FOLLOW: R4.2, TP_F.TP, U1.23 (PC0/ADC0/PTCY/MISO1), U3.13 (-IN), U3.14 (OUT)
V_FOL_ADJ: C12.2, C13.2, FOL.TP, R10.1, U3.12 (+IN)
V_FOL_PWM: F_PWM.TP, R10.2, U1.1 (PD3/OC2B/INT1/PTCXY)
Z_MIN_TRIG: LED.P$4 (BLU), R5.1, R9.1, U1.11 (PD7/PTCXY/AIN1)
Z_OUT: J1.5, R2.2, R9.2
Z_TRG: INT.TP, R15.2, U1.32 (PD2/PTCXY/INT0/OC3B/OC4B)

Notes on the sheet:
ATMega88/168/328
Power
LED's
Holes
Piezo Amp Circuit
Test Points
Connectors
PT100 Amp Circuit
Amplification Stage
Amp Gain Adjustment Ladder
Voltage Follower
Comparator

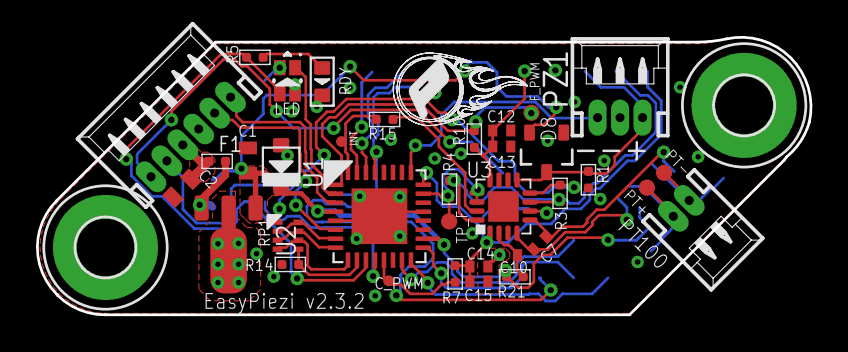
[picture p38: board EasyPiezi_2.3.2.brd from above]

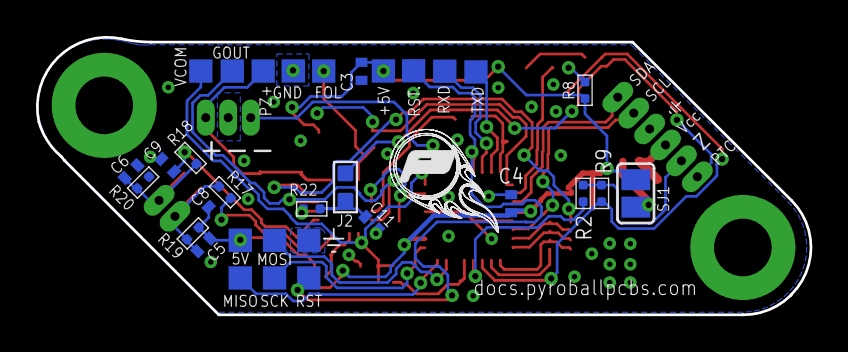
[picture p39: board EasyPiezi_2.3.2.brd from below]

Board: 2 copper layers, 43.0 x 15.4 mm, 71 parts (33 on the bottom side), 41 nets.

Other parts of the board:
U$1, U$2: LOGO-PYR0BALL-SS-6MM

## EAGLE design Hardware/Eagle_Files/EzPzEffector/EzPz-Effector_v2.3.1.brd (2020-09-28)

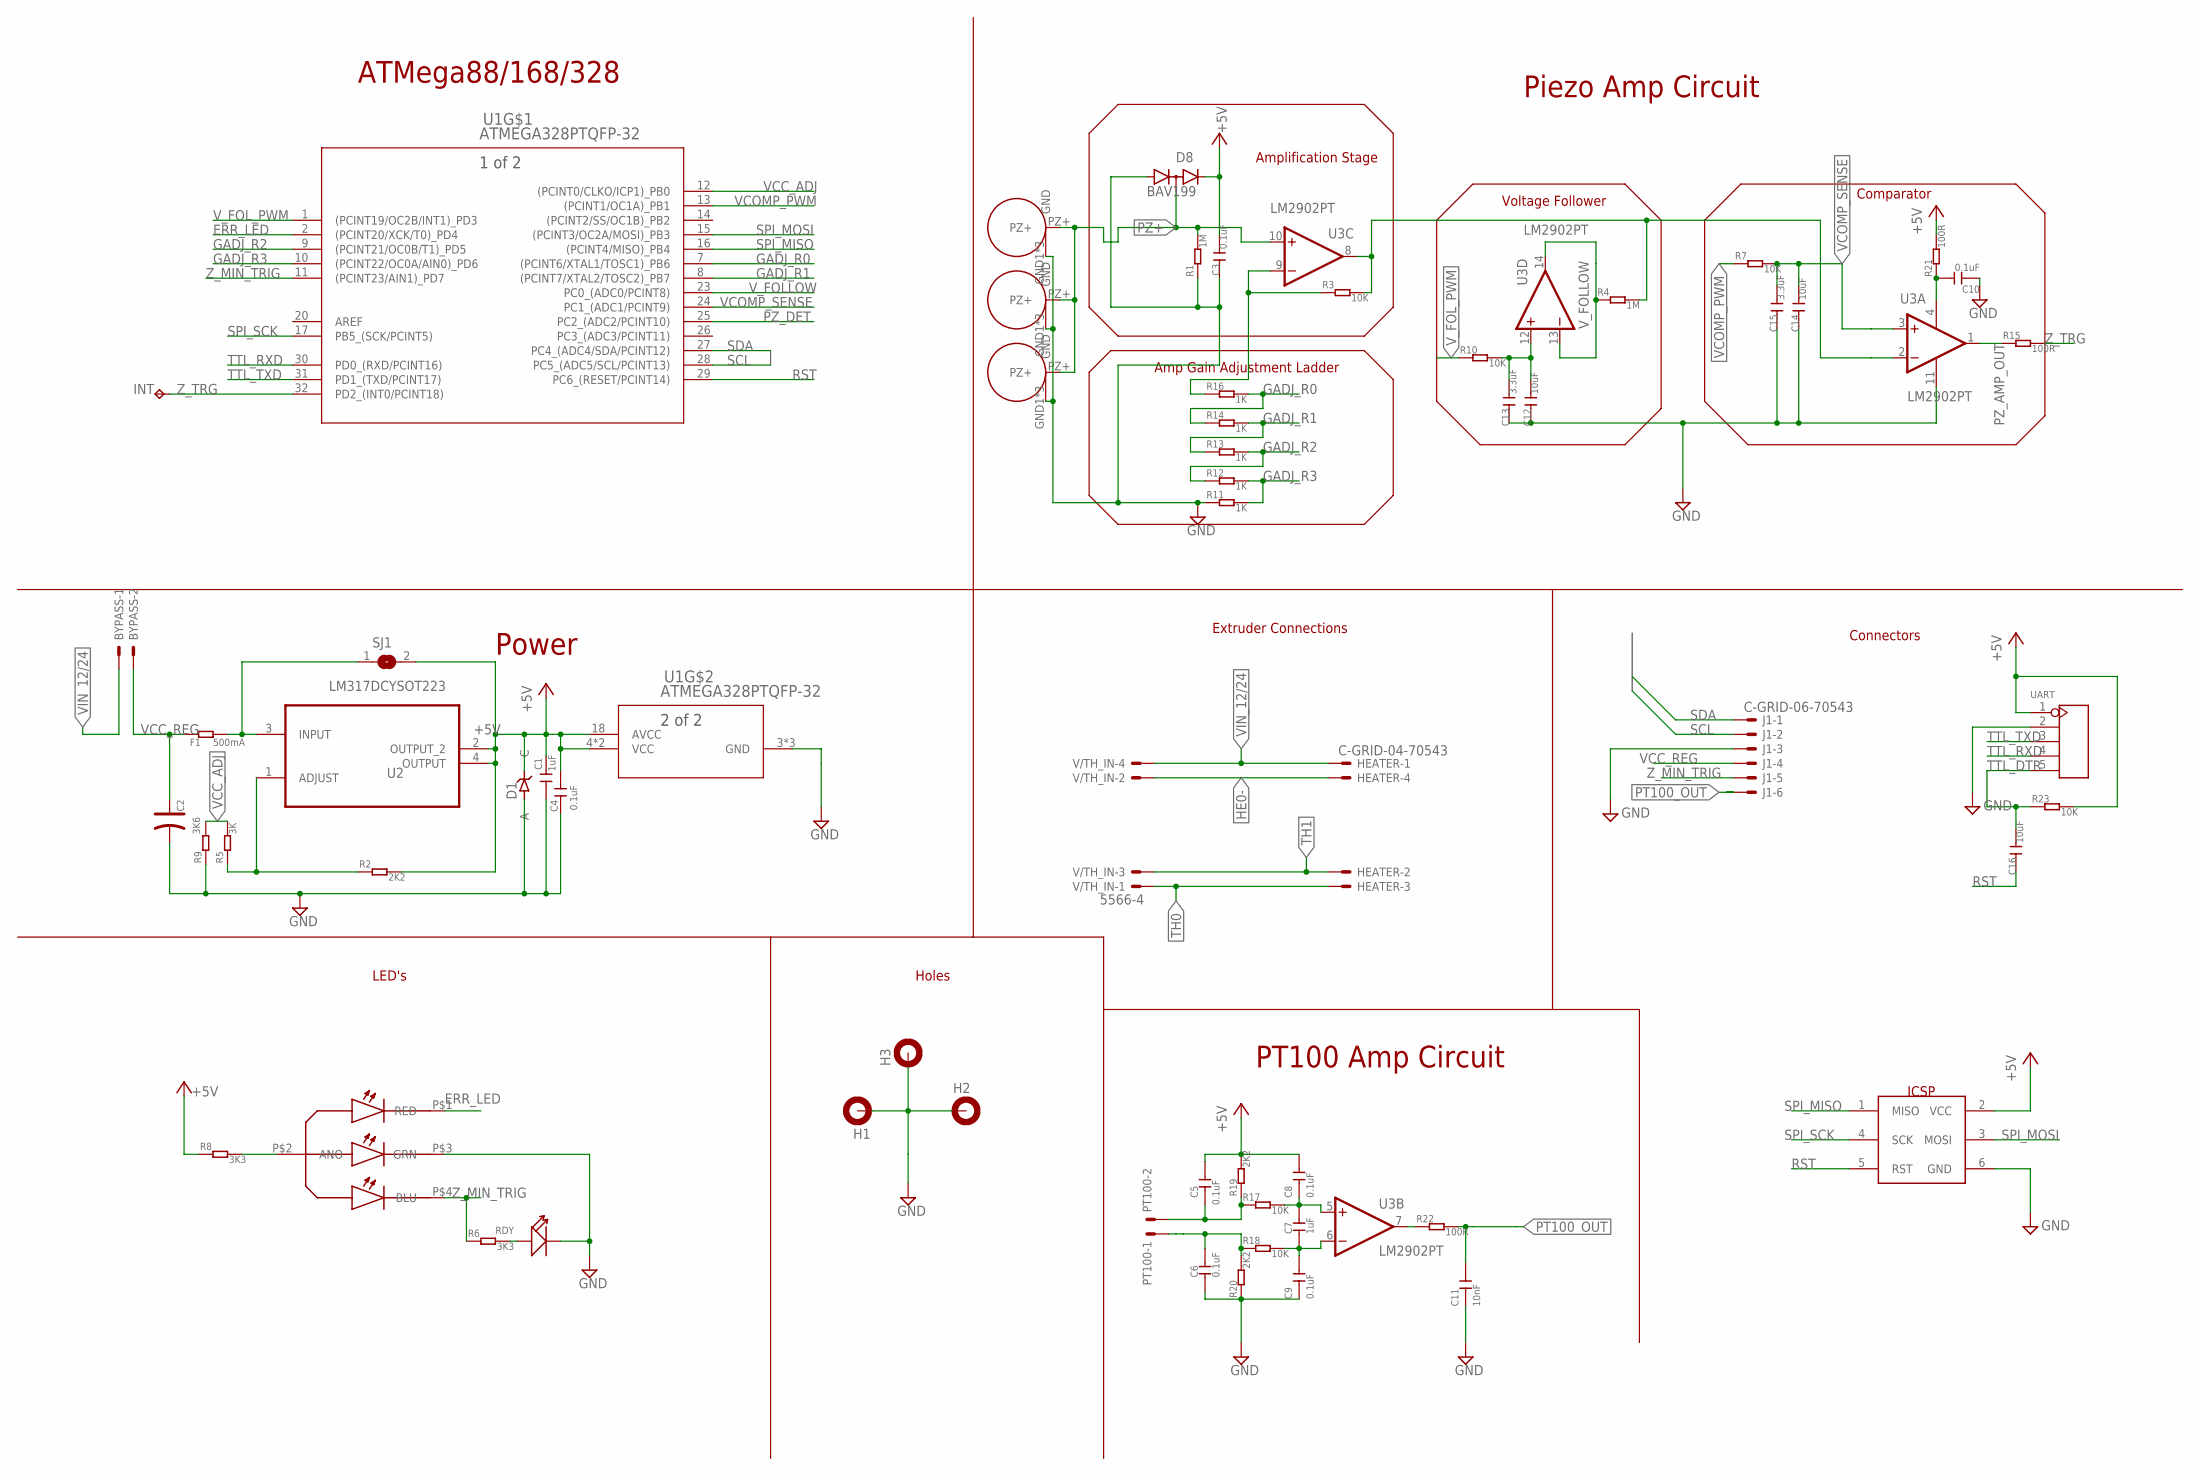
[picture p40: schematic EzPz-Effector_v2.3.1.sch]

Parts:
BYPASS: C-GRID-02-70543; 70543-02
C1, C7: 1uF; C0603K
C2: 100uf; ALU-C-D5.3MM_RIGHT
C3, C4, C5, C6, C8, C9, C10: 0.1uF; C0603K
C11: 10nF; C0603K
C12, C14, C16: 10uF; C0603K
C13, C15: 3.3uF; C0603K
D1: DIODE_ZENER_PLZ5V1C; DO-219AC
D8: BAV199; SOT23
F1: 500mA; SEEED-RESISTOR_R0603
H1, H2, H3: EFFECTOR-ROD-MOUNT; EFFECTOR-45MM-ROD
HEATER: C-GRID-04-70543; 70543-04
ICSP: ICSP_HEADERICSP-2.54MM; ICSP_3X2_2.54_STRAIGHT
INT: TPTP06R; TP06R
J1: C-GRID-06-70543; 70543-06
LED: LED-RGB-COM_ANO0606; 0606_LED
PT100: C-GRID-02-70543; 70543-02
PZ1, PZ2, PZ3: PIEZO-DISK12MM-OFFSET; PIEZO-DISK-12MM-OFFSET
R1, R4: 1M; SEEED-RESISTOR_R0603
R2, R19, R20: 2K2; SEEED-RESISTOR_R0603
R3, R7, R10, R17, R18, R23: 10K; SEEED-RESISTOR_R0603
R5: 3K; SEEED-RESISTOR_R0603
R6, R8: 3K3; SEEED-RESISTOR_R0603
R9: 3K6; SEEED-RESISTOR_R0603
R11, R12, R13, R14, R16: 1K; SEEED-RESISTOR_R0603
R15, R21, R22: 100R; SEEED-RESISTOR_R0603
RDY: SEEED-LED_SMD-LED-CLEAR-BLUE(0603)LED_0603; SEEED-LED_LED-0603
SJ1: SJ
U1: ATMEGA328PTQFP-32; QFP80P900X900X120-32N
U2: LM317DCYSOT223; SOT230P700X180-4N
U3: LM2902PT; SSOP14
UART: JST-2.54MM_5P-2.54JST_2.54MM_5P_F; HDRVR5W64P254_1X5_1270X254X575B
V/TH_IN: 5566-4

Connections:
+5V: C1.2, C3.2, C4.2, C5.2, C8.2, D1.P$2 (C), D8.2 (C), ICSP.2 (VCC), R2.2, R8.1, R19.2, R21.2, R23.2, SJ1.2, U1.4 (VCC), U1.6 (VCC), U1.18 (AVCC), U2.2 (OUTPUT_2), U2.4 (OUTPUT), UART.1
AMP_VCC: C10.2, R21.1, U3.4 (V+)
ERR_LED: LED.P$1 (RED), U1.2 ((PCINT20/XCK/T0)_PD4)
GADJ_R0: R14.1, R16.2, U1.7 ((PCINT6/XTAL1/TOSC1)_PB6)
GADJ_R1: R13.1, R14.2, U1.8 ((PCINT7/XTAL2/TOSC2)_PB7)
GADJ_R2: R12.1, R13.2, U1.9 ((PCINT21/OC0B/T1)_PD5)
GADJ_R3: R11.2, R12.2, U1.10 ((PCINT22/OC0A/AIN0)_PD6)
GAIN_ADJ: R3.1, R16.1, U3.9 (-IN)
GAIN_OUT: R3.2, R4.2, U3.2 (-IN), U3.8 (OUT)
GND: C1.1, C2.-, C3.1, C4.1, C6.1, C9.1, C10.1, C11.1, C12.1, C13.1, C14.1, C15.1, D1.P$1 (A), D8.1 (A), H1.P$1, H1.P$2, H2.P$1, H2.P$2, H3.P$1, H3.P$2, ICSP.6 (GND), J1.3, LED.P$3 (GRN), PZ1.GND1 (GND), PZ1.GND2 (GND), PZ1.GND3 (GND), PZ2.GND1 (GND), PZ2.GND2 (GND), PZ2.GND3 (GND), PZ3.GND1 (GND), PZ3.GND2 (GND), PZ3.GND3 (GND), R1.1, R9.1, R11.1, R20.1, RDY.-, U1.3 (GND), U1.5 (GND), U1.21 (GND), U3.11 (V-), UART.2
HE0-: HEATER.4, V/TH_IN.2
LED_PWR: LED.P$2 (ANO), R8.2
PT100_OUT: C11.2, J1.6, R22.2
PT_AMP: R22.1, U3.7 (OUT)
PT_AMP+: C7.2, C8.1, R17.2, U3.5 (+IN)
PT_AMP-: C7.1, C9.2, R18.2, U3.6 (-IN)
PT_IN+: C5.1, PT100.2, R17.1, R19.1
PT_IN-: C6.2, PT100.1, R18.1, R20.2
PZ+: D8.3 (AC), PZ1.PZ+, PZ2.PZ+, PZ3.PZ+, R1.2, U3.10 (+IN)
PZ_AMP_OUT: R15.1, U3.1 (OUT)
PZ_DET: U1.25 (PC2_(ADC2/PCINT10))
RDY_LED: R6.2, RDY.+
REG_ADJ: R2.1, R5.1, U2.1 (ADJUST)
RST: C16.1, ICSP.5 (RST), U1.29 (PC6_(RESET/PCINT14))
SCL: J1.2, U1.28 (PC5_(ADC5/SCL/PCINT13))
SDA: J1.1, U1.27 (PC4_(ADC4/SDA/PCINT12))
SPI_MISO: ICSP.1 (MISO), U1.16 ((PCINT4/MISO)_PB4)
SPI_MOSI: ICSP.3 (MOSI), U1.15 ((PCINT3/OC2A/MOSI)_PB3)
SPI_SCK: ICSP.4 (SCK), U1.17 (PB5_(SCK/PCINT5))
TH0: HEATER.3, V/TH_IN.1
TH1: HEATER.2, V/TH_IN.3
TTL_DTR: C16.2, R23.1, UART.5
TTL_RXD: U1.30 (PD0_(RXD/PCINT16)), UART.4
TTL_TXD: U1.31 (PD1_(TXD/PCINT17)), UART.3
VCC_ADJ: R5.2, R9.2, U1.12 ((PCINT0/CLKO/ICP1)_PB0)
VCC_FUSE: F1.2, SJ1.1, U2.3 (INPUT)
VCC_REG: BYPASS.2, C2.+, F1.1, J1.4
VCOMP_PWM: R7.1, U1.13 ((PCINT1/OC1A)_PB1)
VCOMP_SENSE: C14.2, C15.2, R7.2, U1.24 (PC1_(ADC1/PCINT9)), U3.3 (+IN)
VIN_12/24: BYPASS.1, HEATER.1, V/TH_IN.4
V_FOLLOW: R4.1, U1.23 (PC0_(ADC0/PCINT8)), U3.13 (-IN), U3.14 (OUT)
V_FOL_ADJ: C12.2, C13.2, R10.2, U3.12 (+IN)
V_FOL_PWM: R10.1, U1.1 ((PCINT19/OC2B/INT1)_PD3)
Z_MIN_TRIG: J1.5, LED.P$4 (BLU), R6.1, U1.11 ((PCINT23/AIN1)_PD7)
Z_TRG: INT.TP, R15.2, U1.32 (PD2_(INT0/PCINT18))

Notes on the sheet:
ATMega88/168/328
Power
LED's
Holes
Piezo Amp Circuit
Extruder Connections
Connectors
PT100 Amp Circuit
Amplification Stage
Amp Gain Adjustment Ladder
Voltage Follower
Comparator

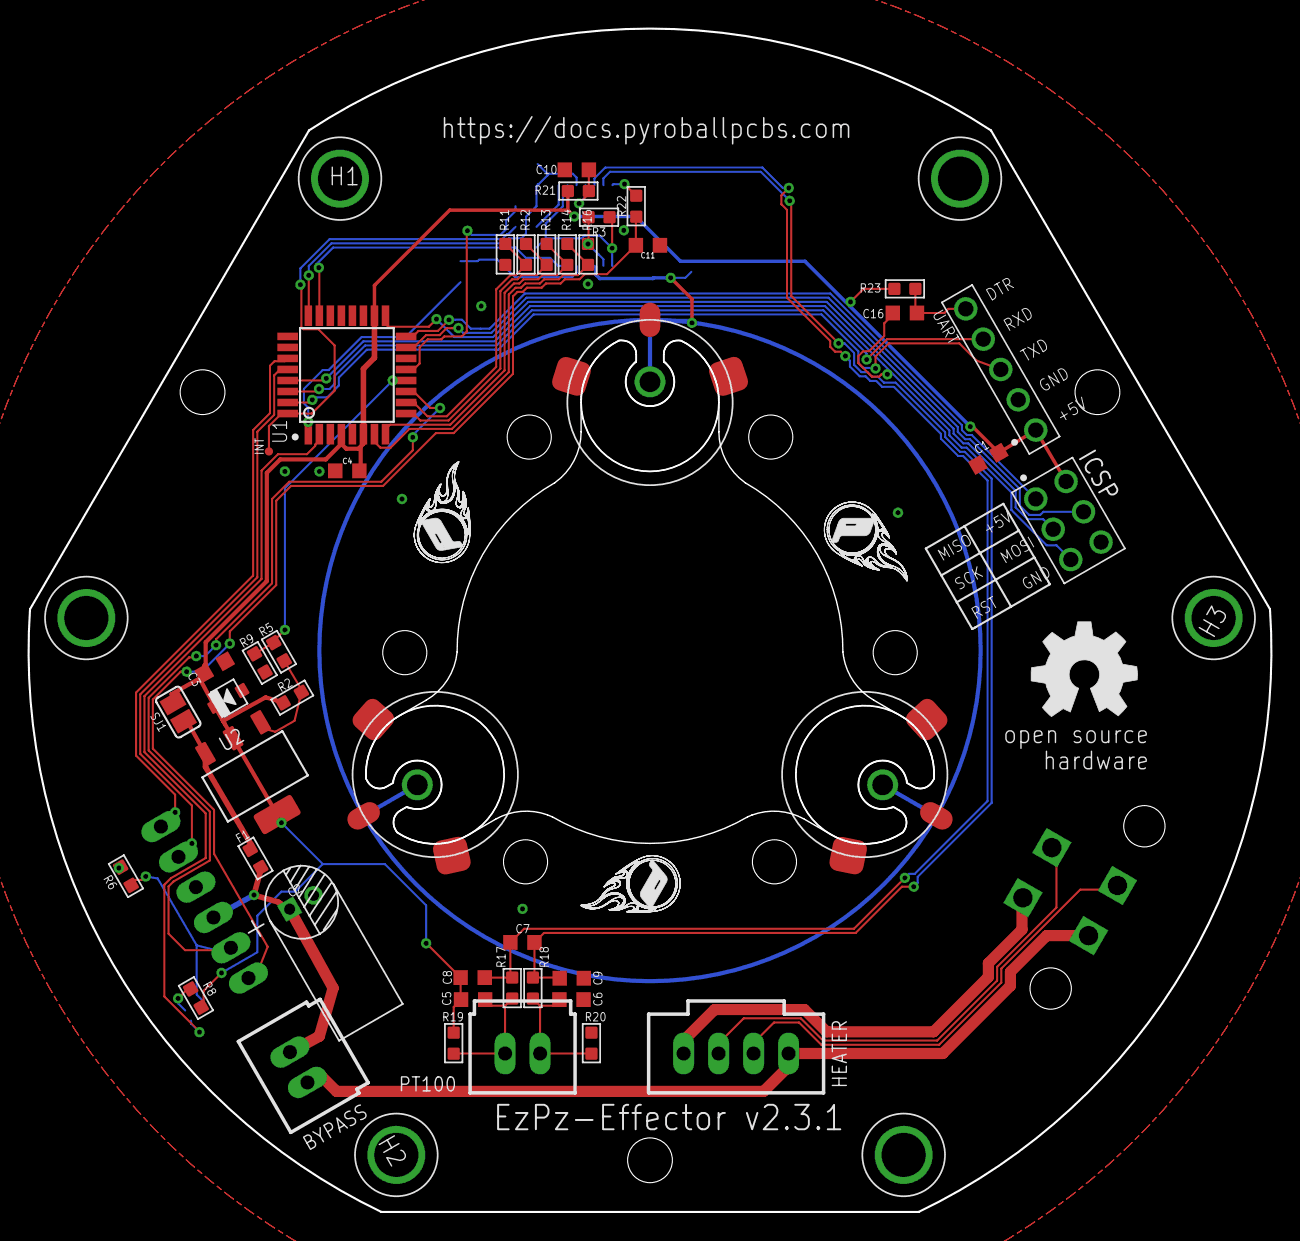
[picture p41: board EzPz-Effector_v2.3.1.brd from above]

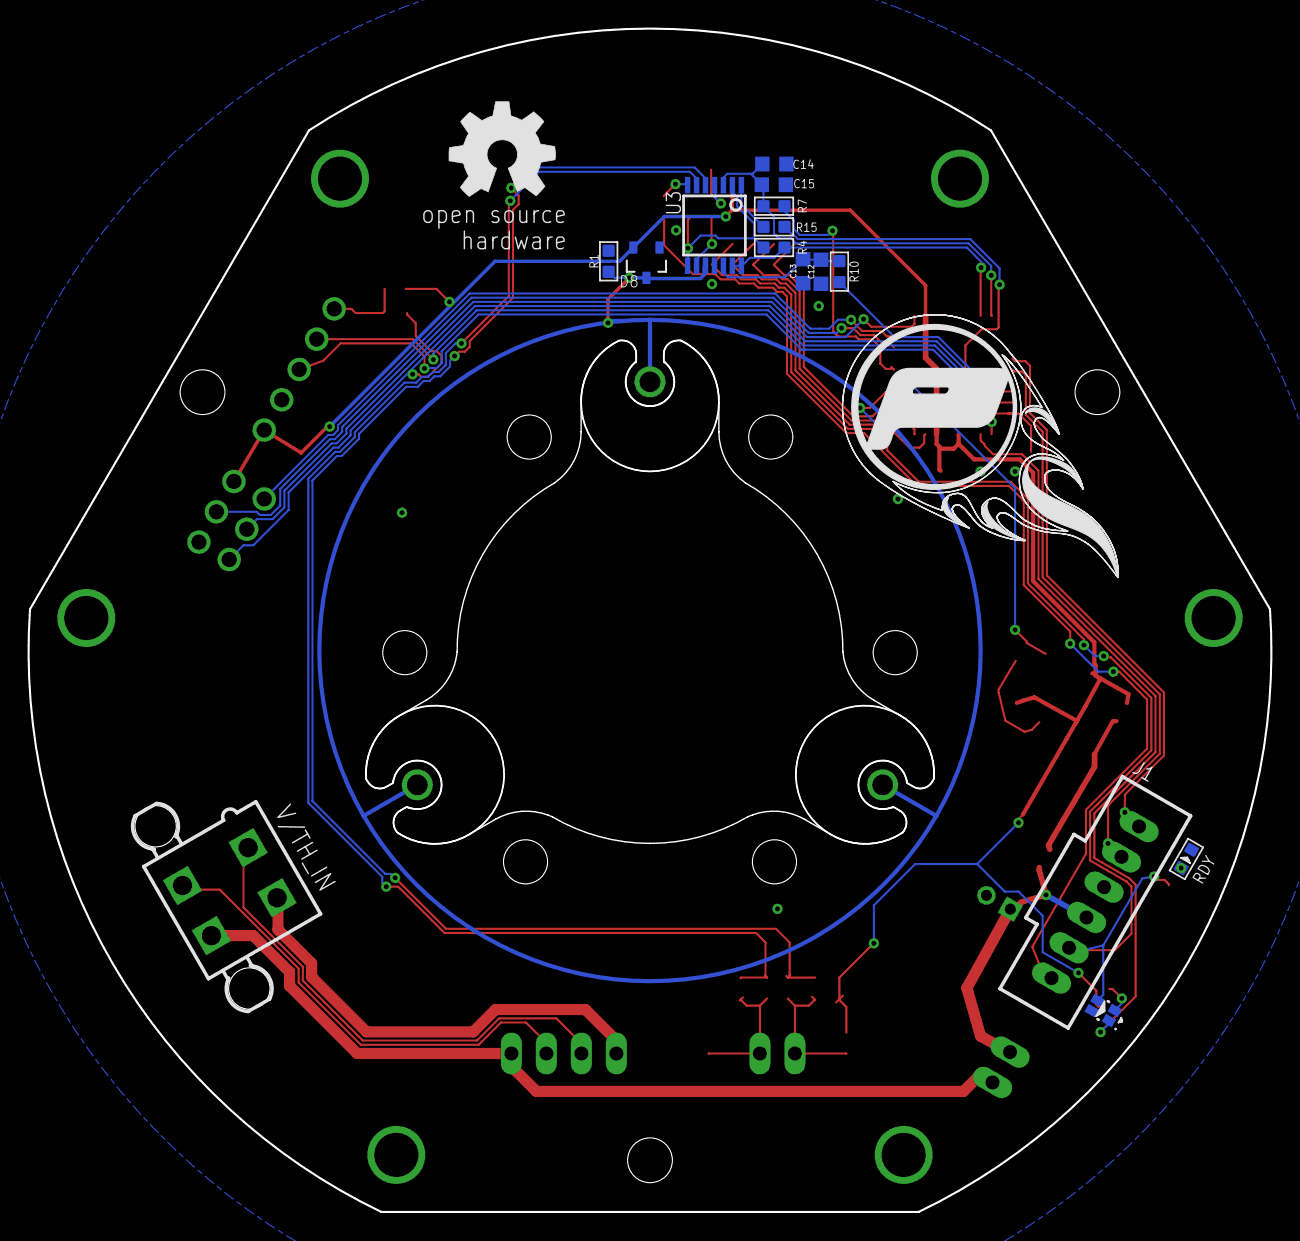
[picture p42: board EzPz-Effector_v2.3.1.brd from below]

Board: 2 copper layers, 90.2 x 85.9 mm, 68 parts (17 on the bottom side), 44 nets.

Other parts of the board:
U$1: LOGO-PYR0BALL-SS-20MM
U$2, U$3, U$4: LOGO-PYR0BALL-SS-6MM
U$5, U$6: OSHW_8MM

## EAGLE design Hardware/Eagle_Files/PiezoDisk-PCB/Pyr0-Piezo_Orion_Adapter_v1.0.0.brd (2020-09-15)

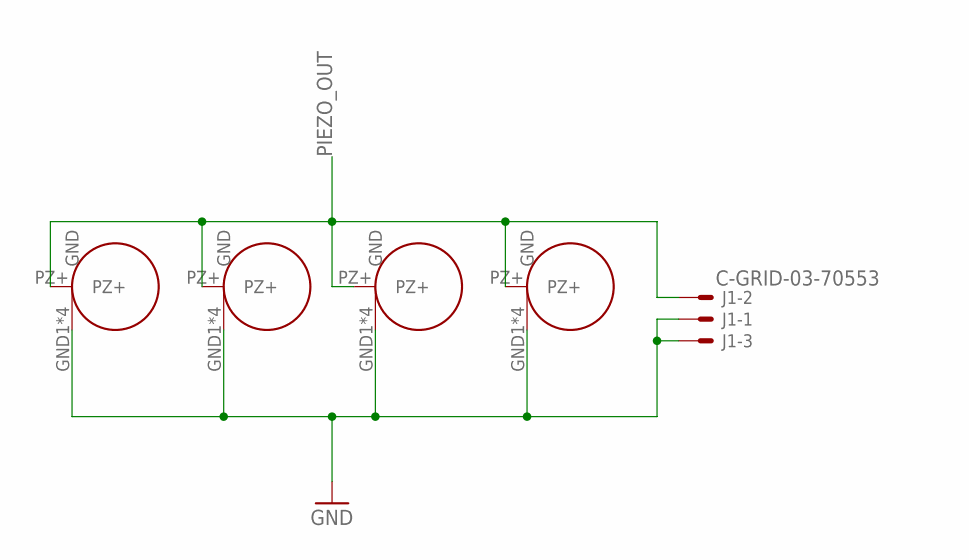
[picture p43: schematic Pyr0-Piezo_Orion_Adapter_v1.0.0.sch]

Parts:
J1: C-GRID-03-70553; 70553-03
U$1, U$2, U$3, U$4: PIEZO-DISK12MM; PIEZO-DISK-12MM

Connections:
GND: J1.1, J1.3, U$1.GND1 (GND), U$1.GND2 (GND), U$1.GND3 (GND), U$1.GND4 (GND), U$2.GND1 (GND), U$2.GND2 (GND), U$2.GND3 (GND), U$2.GND4 (GND), U$3.GND1 (GND), U$3.GND2 (GND), U$3.GND3 (GND), U$3.GND4 (GND), U$4.GND1 (GND), U$4.GND2 (GND), U$4.GND3 (GND), U$4.GND4 (GND)
PIEZO_OUT: J1.2, U$1.PZ+, U$2.PZ+, U$3.PZ+, U$4.PZ+

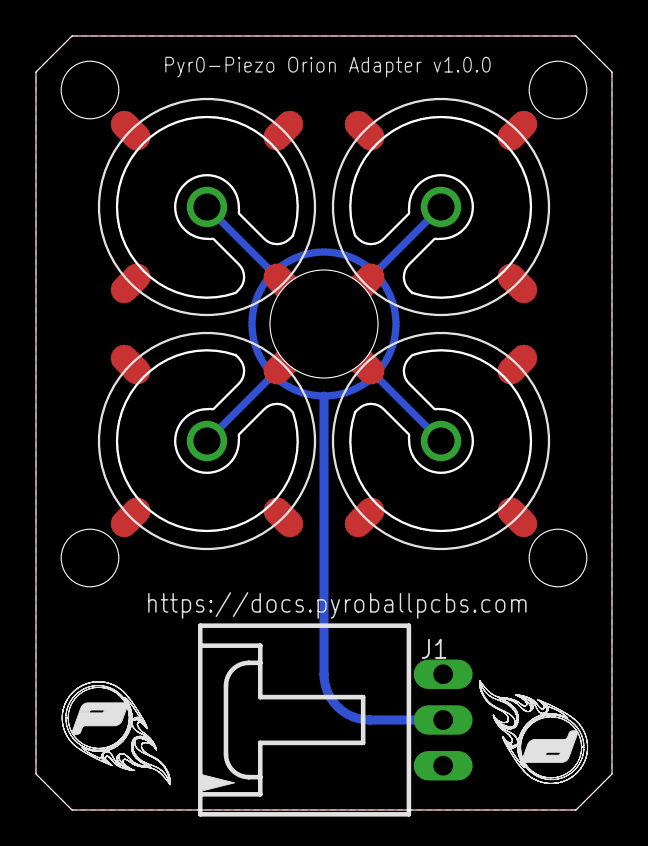
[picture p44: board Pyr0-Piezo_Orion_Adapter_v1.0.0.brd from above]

Board: 2 copper layers, 32.0 x 43.0 mm, 7 parts (0 on the bottom side), 2 nets.

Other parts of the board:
U$5, U$6: LOGO-PYR0BALL-SS-6MM

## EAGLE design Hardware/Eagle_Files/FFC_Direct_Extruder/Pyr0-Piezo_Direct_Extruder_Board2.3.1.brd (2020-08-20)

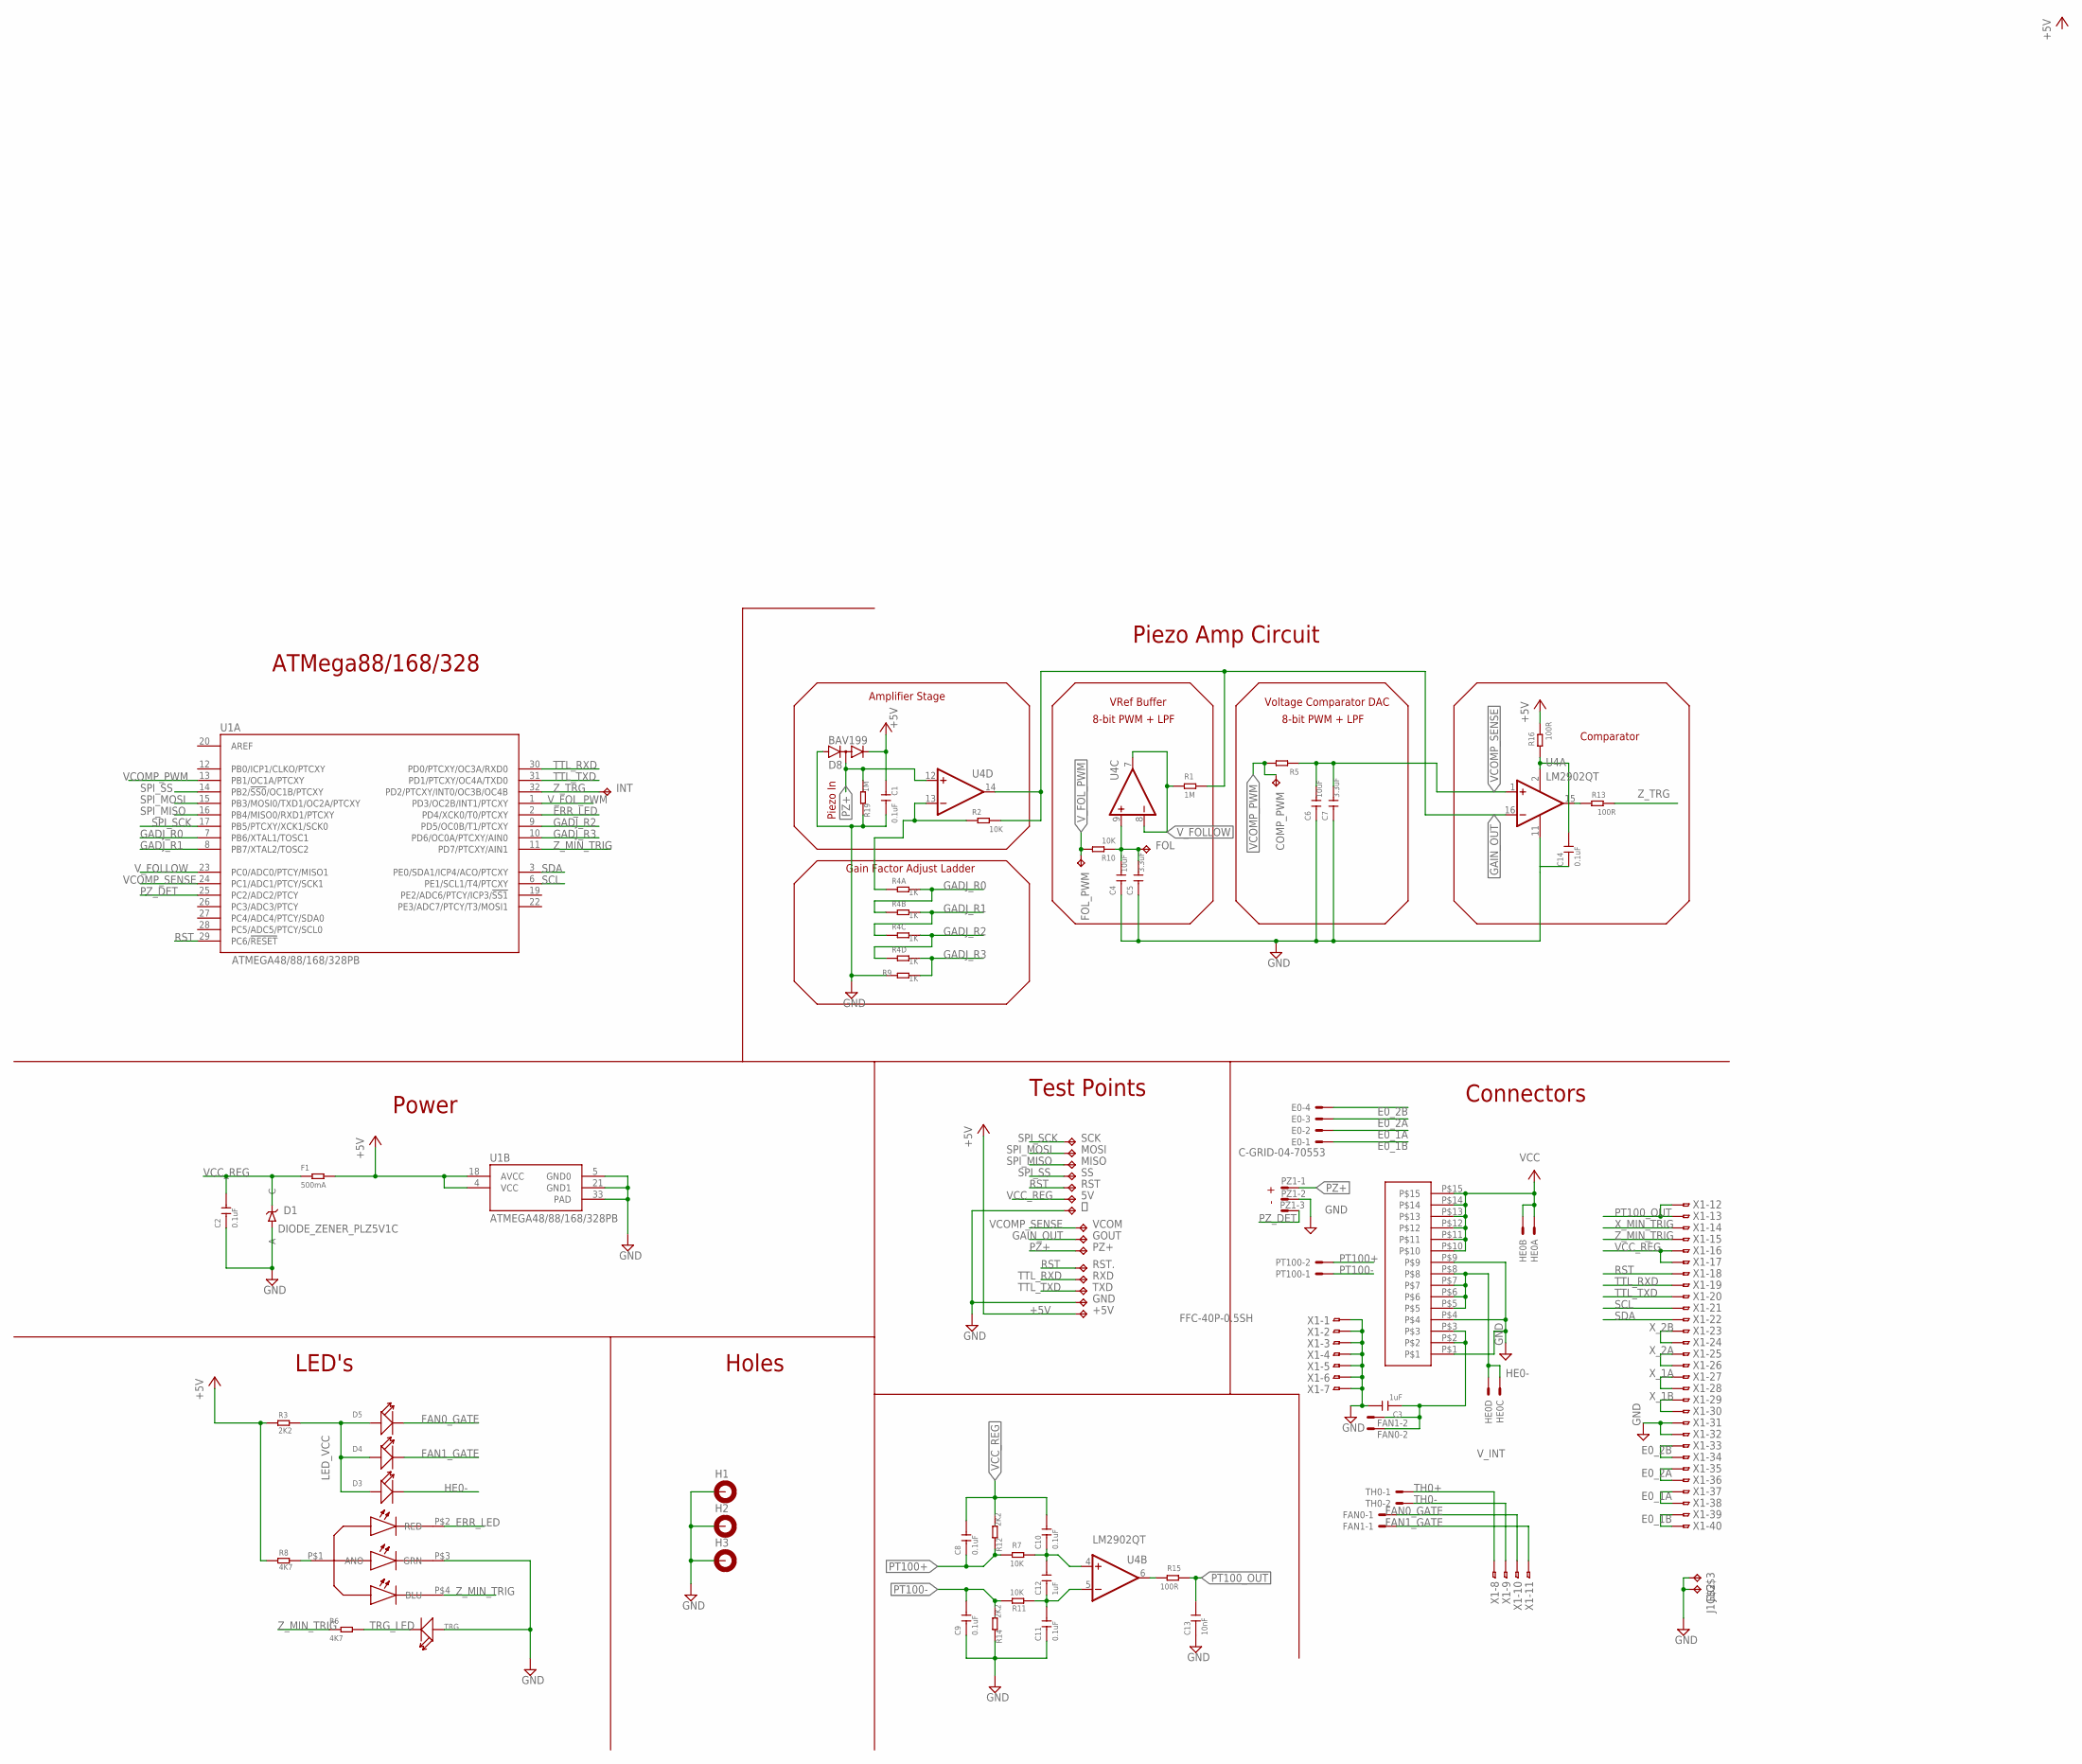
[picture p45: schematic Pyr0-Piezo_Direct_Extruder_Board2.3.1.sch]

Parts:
5V: TPTP13SQ; TP13SQ
+5V: TPTP13SQ; TP13SQ
C1: 0.1uF; CAPC2012X130
C2, C8, C9, C10, C11, C14: 0.1uF; CAPC1005X50
C3: 1uF; CAPC1609X80
C4, C6: 10uF; CAPC1005X50
C5, C7: 3.3uF; CAPC1609X80
C12: 1uF; CAPC1005X50
C13: 10nF; CAPC1005X50
COMP_PWM: TPTP09R; TP09R
D1: DIODE_ZENER_PLZ5V1C; DO-219AC
D2: LED-RGB-COM_ANO4PLCC; 4PLCC
D3, D4, D5: SEEED-LED_SMD-LED-CLEAR-BLUE(0603)LED_0603; SEEED-LED_LED-0603
D8: BAV199; SOT23
E0: C-GRID-04-70553; 70553-04
F1: 500mA; SEEED-RESISTOR_R0603
FAN0, FAN1: CON-MOLEX-2P-1.27MM048; 53048-02
FOL: TPTP13SQ; TP13SQ
FOL_PWM: TPTP09R; TP09R
GND: TPTP13SQ; TP13SQ
GOUT: TPTP13SQ; TP13SQ
H1, H2, H3: HOLES_MOUNT-PAD-ROUND3.2; HOLES_3,2-PAD
HE0: JST-2.54-2X2JST-DUPONT-2.54-2X2; HDRRAR4W64P254_2X2_556X736X556B
INT: TPTP13R; TP13R
J1: FFC-15P-1MM
MISO: TPTP13SQ; TP13SQ
MOSI: TPTP13SQ; TP13SQ
PT100: CON-MOLEX-2P-1.27MM048; 53048-02
PZ1: CON-MOLEX-3P-1.25MM048; 53048-03
PZ+: TPTP13SQ; TP13SQ
R1, R19: 1M; R0402
R2, R7, R10, R11: 10K; R0402
R3, R12, R14: 2K2; R0402
R4: 1K; EXBN8V
R5: 0R; R0402
R6, R8: 4K7; R0402
R9: 1K; R0402
R13, R15, R16: 100R; R0402
RST, RST.: TPTP13SQ; TP13SQ
RXD: TPTP13SQ; TP13SQ
SCK: TPTP13SQ; TP13SQ
SS: TPTP06R; TP06R
TH0: CON-MOLEX-2P-1.27MM048; 53048-02
TRG: SEEED-LED_SMD-LED-CLEAR-BLUE(0603)LED_0603; SEEED-LED_LED-0603
TXD: TPTP13SQ; TP13SQ
U1: ATMEGA48/88/168/328PB; QFN50P500X500X90-33N
U4: LM2902QT; QFN16
VCOM: TPTP13SQ; TP13SQ
X1: FFC-40P-0.5SH; FH12-40S-0.5SH
⏚: TPTP13SQ; TP13SQ

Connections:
+5V: +5V.TP, C1.1, D8.2 (C), F1.2, R3.1, R8.1, R16.2, U1.4 (VCC), U1.18 (AVCC)
COMP_VCC: C14.2, R16.1, U4.2 (V+)
E0_1A: E0.2, X1.37 (1), X1.38 (1)
E0_1B: E0.1, X1.39 (1), X1.40 (1)
E0_2A: E0.3, X1.35 (1), X1.36 (1)
E0_2B: E0.4, X1.33 (1), X1.34 (1)
ERR_LED: D2.P$2 (RED), U1.2 (PD4/XCK0/T0/PTCXY)
FAN0_GATE: D5.-, FAN0.1, X1.10 (1)
FAN1_GATE: D4.-, FAN1.1, X1.11 (1)
GADJ_R0: R4.2 (1), R4.8 (2), U1.7 (PB6/XTAL1/TOSC1)
GADJ_R1: R4.3 (1), R4.7 (2), U1.8 (PB7/XTAL2/TOSC2)
GADJ_R2: R4.4 (1), R4.6 (2), U1.9 (PD5/OC0B/T1/PTCXY)
GADJ_R3: R4.5 (2), R9.2, U1.10 (PD6/OC0A/PTCXY/AIN0)
GAIN_FB: R2.1, R4.1, U4.13 (-IN)
GAIN_OUT: GOUT.TP, R1.2, R2.2, U4.14 (OUT), U4.16 (-IN)
GND: C1.2, C2.1, C3.2, C4.1, C5.1, C6.1, C7.1, C9.1, C11.1, C13.1, C14.1, D1.P$1 (A), D2.P$3 (GRN), D8.1 (A), GND.TP, H1.B3,2, H2.B3,2, H3.B3,2, J1.P$1, J1.P$4, J1.P$9, J1.P$16 (TP), J1.P$17 (TP), PZ1.2, R9.1, R14.1, R19.1, TRG.+, U1.5 (GND0), U1.21 (GND1), U1.33 (PAD), U4.11 (V-), X1.1, X1.2 (1), X1.3 (1), X1.4 (1), X1.5 (1), X1.6 (1), X1.7 (1), X1.31 (1), X1.32 (1), ⏚.TP
HE0-: D3.-, HE0.3, HE0.4, J1.P$5, J1.P$6, J1.P$7, J1.P$8
LED_VCC: D3.+, D4.+, D5.+, R3.2
PT100+: C8.1, PT100.2, R7.2, R12.1
PT100-: C9.2, PT100.1, R11.2, R14.2
PT100_AMP+: C10.1, C12.2, R7.1, U4.4 (+IN)
PT100_AMP-: C11.2, C12.1, R11.1, U4.5 (-IN)
PT100_OUT: C13.2, R15.1, X1.12 (1), X1.13 (1)
PT100_R: R15.2, U4.6 (OUT)
PZ+: D8.3 (AC), PZ1.1, PZ+.TP, R19.2, U4.12 (+IN)
PZ_AMP_OUT: R13.1, U4.15 (OUT)
PZ_DET: PZ1.3, U1.25 (PC2/ADC2/PTCY)
RGB_VCC: D2.P$1 (ANO), R8.2
RST: RST.TP, RST..TP, U1.29 (PC6/!RESET!), X1.18 (1)
SCL: U1.6 (PE1/SCL1/T4/PTCXY), X1.21 (1)
SDA: U1.3 (PE0/SDA1/ICP4/ACO/PTCXY), X1.22 (1)
SPI_MISO: MISO.TP, U1.16 (PB4/MISO0/RXD1/PTCXY)
SPI_MOSI: MOSI.TP, U1.15 (PB3/MOSI0/TXD1/OC2A/PTCXY)
SPI_SCK: SCK.TP, U1.17 (PB5/PTCXY/XCK1/SCK0)
SPI_SS: SS.TP, U1.14 (PB2/!SS0!/OC1B/PTCXY)
TH0+: TH0.1, X1.8 (1)
TH0-: TH0.2, X1.9 (1)
TRG_LED: R6.2, TRG.-
TTL_RXD: RXD.TP, U1.30 (PD0/PTCXY/OC3A/RXD0), X1.19 (1)
TTL_TXD: TXD.TP, U1.31 (PD1/PTCXY/OC4A/TXD0), X1.20 (1)
VCC: HE0.1, HE0.2, J1.P$10, J1.P$11, J1.P$12, J1.P$13, J1.P$14, J1.P$15
VCC_REG: 5V.TP, C2.2, C8.2, C10.2, D1.P$2 (C), F1.1, R12.2, X1.16 (1), X1.17 (1)
VCOMP_PWM: COMP_PWM.TP, R5.2, U1.13 (PB1/OC1A/PTCXY)
VCOMP_SENSE: C6.2, C7.2, R5.1, U1.24 (PC1/ADC1/PTCY/SCK1), U4.1 (+IN), VCOM.TP
VREF_IN: C4.2, C5.2, FOL.TP, R10.1, U4.9 (+IN)
V_FOLLOW: R1.1, U1.23 (PC0/ADC0/PTCY/MISO1), U4.7 (OUT), U4.8 (-IN)
V_FOL_PWM: FOL_PWM.TP, R10.2, U1.1 (PD3/OC2B/INT1/PTCXY)
V_INT: C3.1, FAN0.2, FAN1.2, J1.P$2, J1.P$3
X_1A: X1.27 (1), X1.28 (1)
X_1B: X1.29 (1), X1.30 (1)
X_2A: X1.25 (1), X1.26 (1)
X_2B: X1.23 (1), X1.24 (1)
X_MIN_TRIG: X1.14 (1)
Z_MIN_TRIG: D2.P$4 (BLU), R6.1, U1.11 (PD7/PTCXY/AIN1), X1.15 (1)
Z_TRG: INT.TP, R13.2, U1.32 (PD2/PTCXY/INT0/OC3B/OC4B)

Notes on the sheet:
ATMega88/168/328
Power
LED's
Holes
Piezo Amp Circuit
Test Points
Connectors
VRef Buffer
Voltage Comparator DAC
Comparator
Piezo In
Amplifier Stage
8-bit PWM + LPF
- +
Gain Factor Adjust Ladder

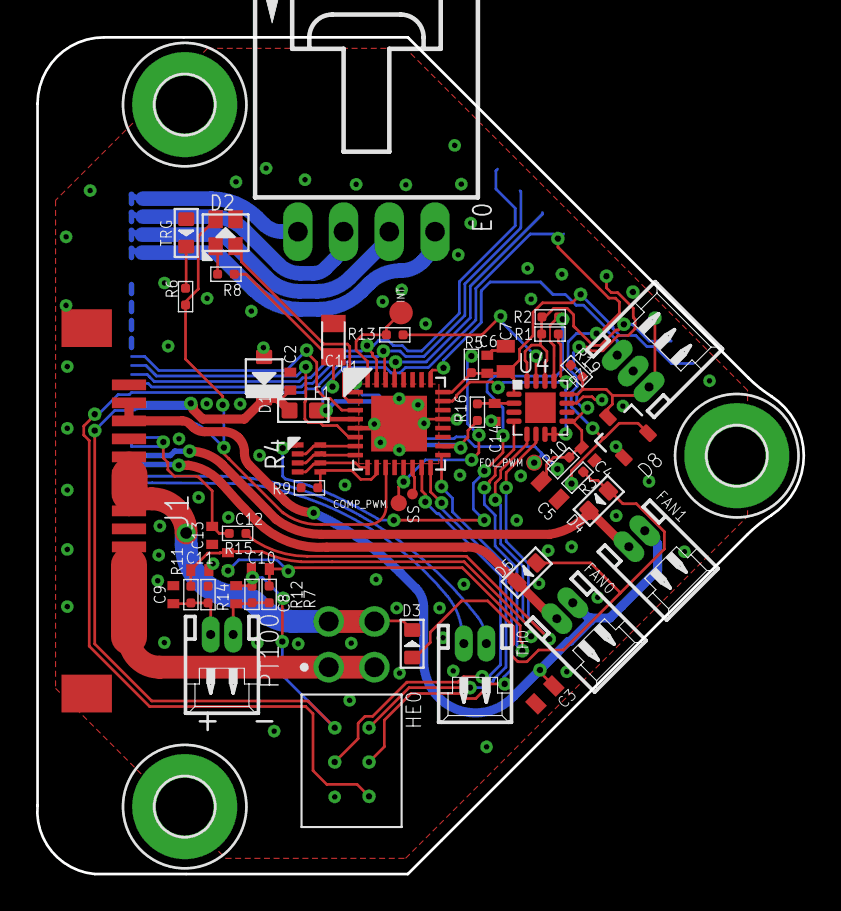
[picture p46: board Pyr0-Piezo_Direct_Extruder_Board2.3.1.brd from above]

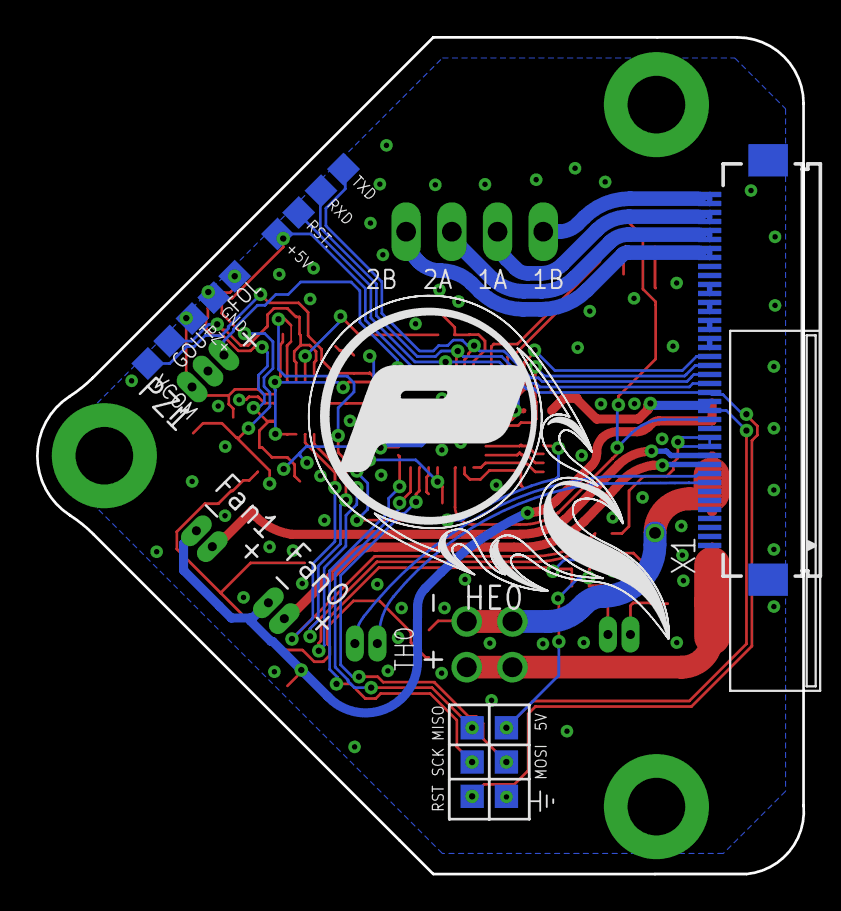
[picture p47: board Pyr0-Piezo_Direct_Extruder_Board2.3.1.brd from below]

Board: 2 copper layers, 42.6 x 46.5 mm, 73 parts (17 on the bottom side), 54 nets.

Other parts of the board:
U$1: LOGO-PYR0BALL-SS-20MM

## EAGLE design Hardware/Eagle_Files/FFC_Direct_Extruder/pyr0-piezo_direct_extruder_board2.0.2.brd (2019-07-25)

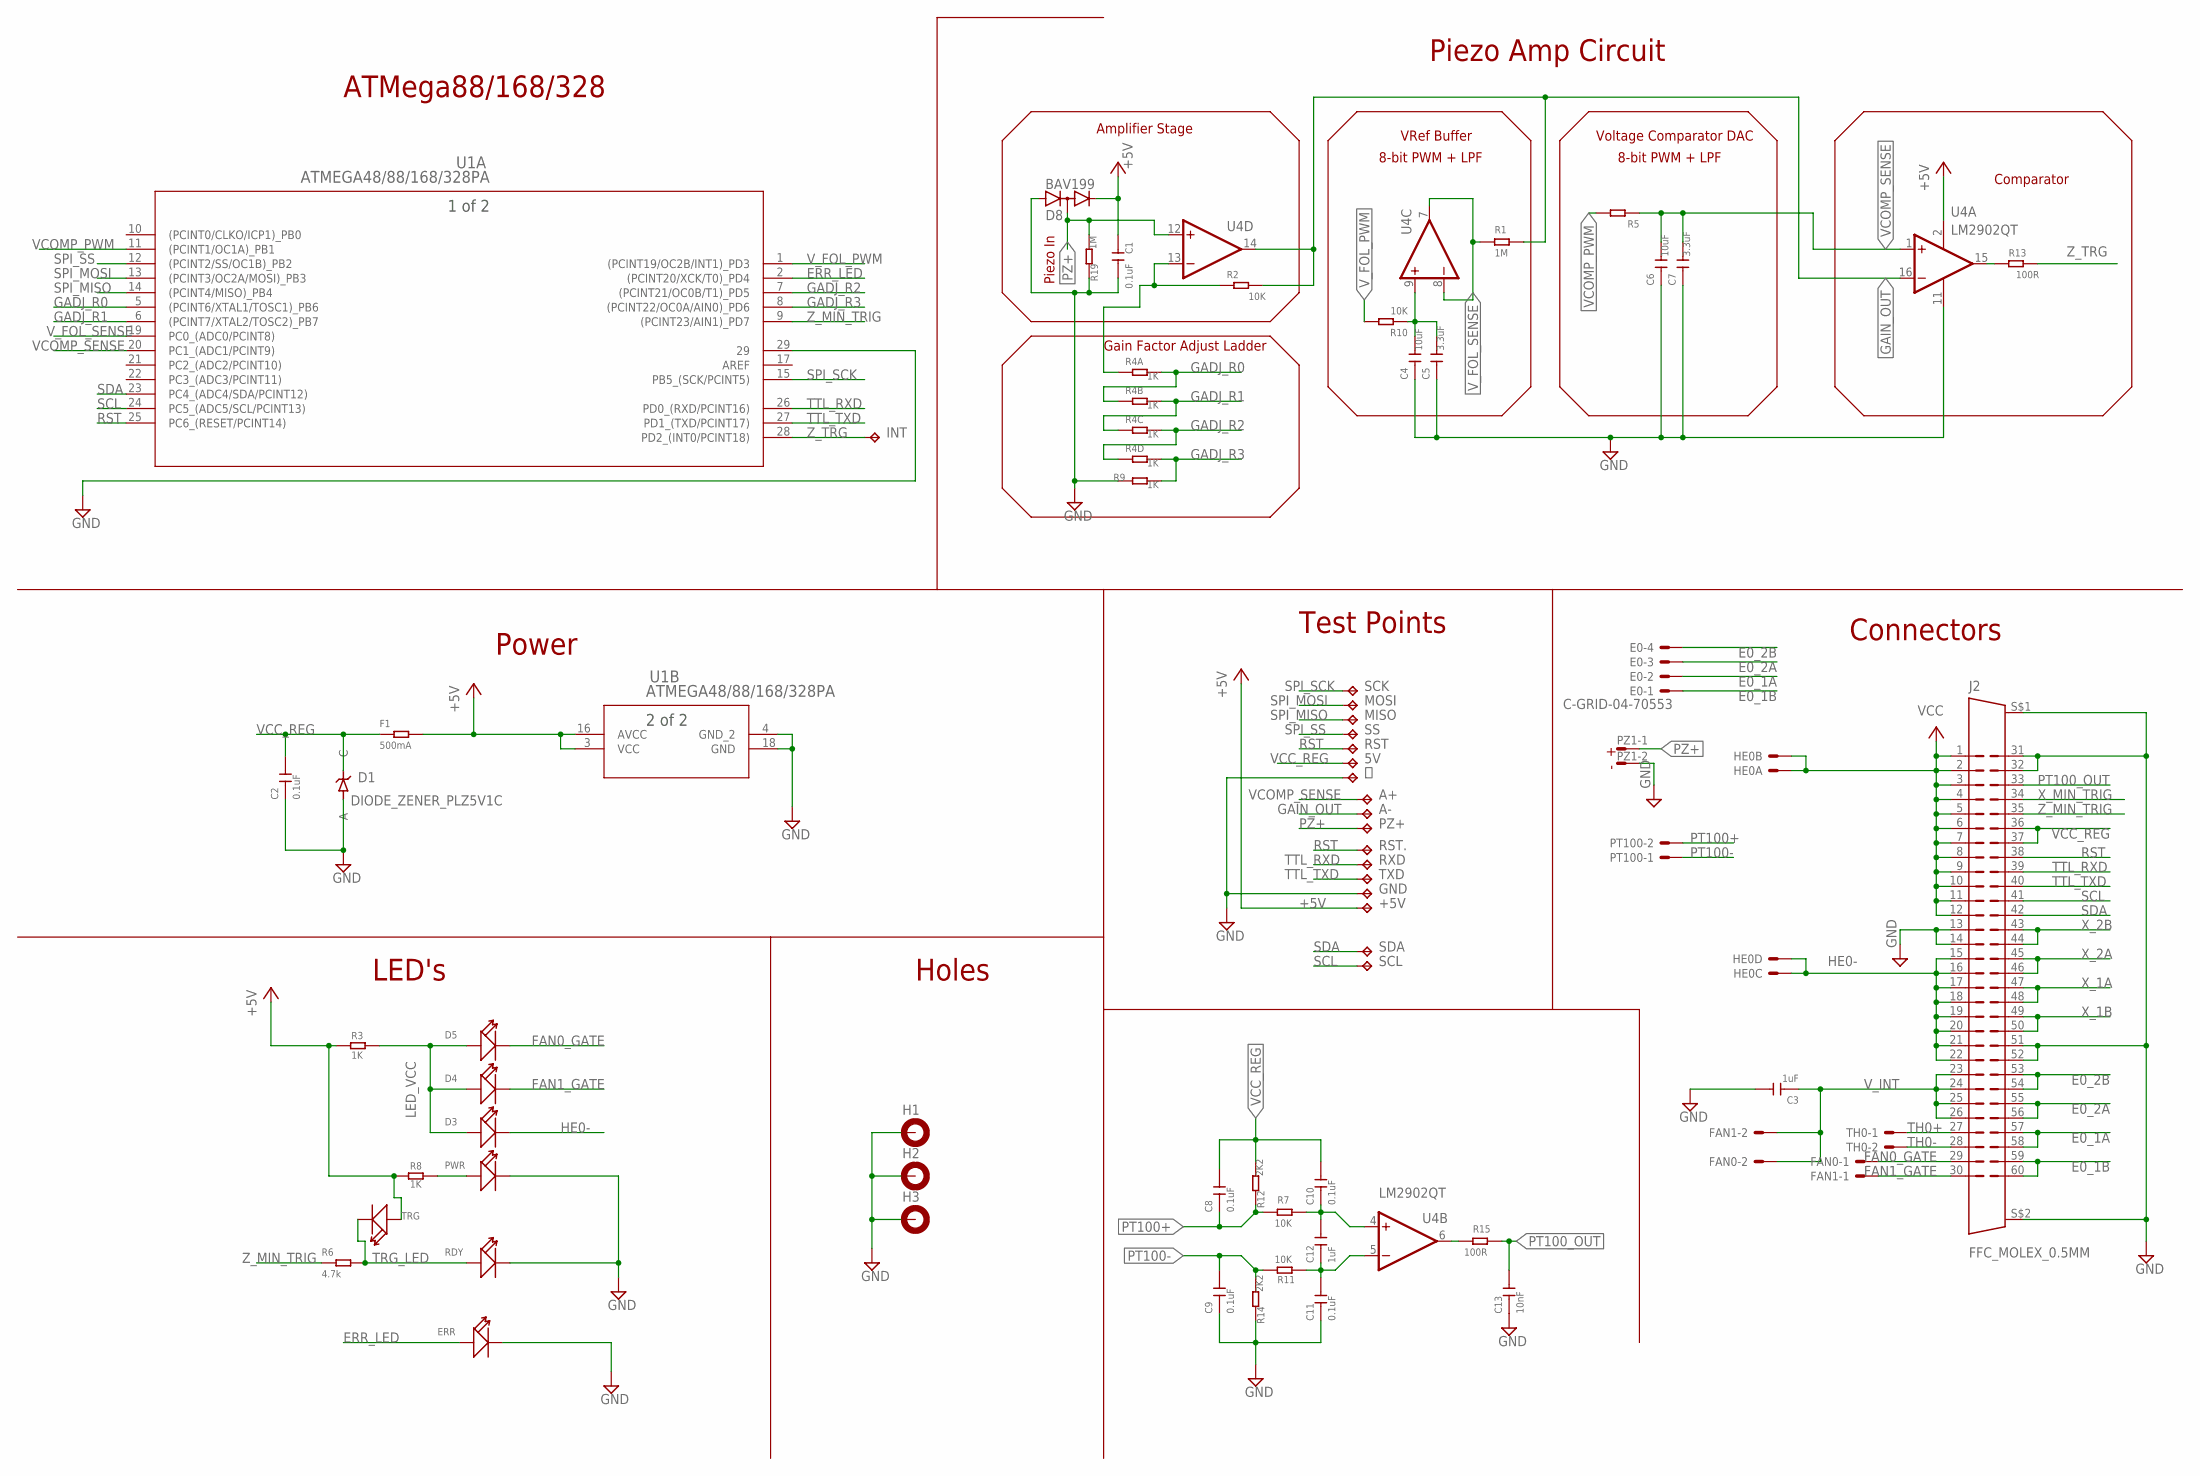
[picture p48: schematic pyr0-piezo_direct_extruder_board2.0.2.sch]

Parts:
5V: TPTP13SQ; TP13SQ
+5V: TPTP13SQ; TP13SQ
A+: TPTP13SQ; TP13SQ
A-: TPTP13SQ; TP13SQ
C1, C2, C8, C9, C10, C11: 0.1uF; CAPC1005X50
C3: 1uF; CAPC1609X80
C4, C6: 10uF; CAPC1005X50
C5, C7: 3.3uF; CAPC1609X80
C12: 1uF; CAPC1005X50
C13: 10nF; CAPC1005X50
D1: DIODE_ZENER_PLZ5V1C; DO-219AC
D3, D4, D5: SEEED-LED_SMD-LED-CLEAR-BLUE(0603)LED_0603; SEEED-LED_LED-0603
D8: BAV199; SOT23
E0: C-GRID-04-70553; 70553-04
ERR: SEEED-LED_SMD-LED-CLEAR-BLUE(0603)LED_0603; SEEED-LED_LED-0603
F1: 500mA; SEEED-RESISTOR_R0603
FAN0, FAN1: CON-MOLEX-2P-1.27MM048; 53048-02
GND: TPTP13SQ; TP13SQ
H1, H2, H3: HOLES_MOUNT-PAD-ROUND3.2; HOLES_3,2-PAD
HE0: JST-2.54-2X2JST-DUPONT-2.54-2X2; HDRRAR4W64P254_2X2_556X736X556B
INT: TPTP06R; TP06R
J2: FFC_MOLEX_0.5MM; FFC-60P_0.5_MOLEX_505110-6091
MISO: TPTP13SQ; TP13SQ
MOSI: TPTP13SQ; TP13SQ
PT100: CON-MOLEX-2P-1.27MM048; 53048-02
PWR: SEEED-LED_SMD-LED-CLEAR-BLUE(0603)LED_0603; SEEED-LED_LED-0603
PZ1: CON-MOLEX-2P-1.27MM048; 53048-02
PZ+: TPTP13SQ; TP13SQ
R1, R19: 1M; R0402
R2, R7, R10, R11: 10K; R0402
R3, R8, R9: 1K; R0402
R4: 1K; EXBN8V
R5: 10K; SEEED-RESISTOR_R0603
R6: 4.7k; R0402
R12, R14: 2K2; R0402
R13, R15: 100R; R0402
RDY: SEEED-LED_SMD-LED-CLEAR-BLUE(0603)LED_0603; SEEED-LED_LED-0603
RST, RST.: TPTP13SQ; TP13SQ
RXD: TPTP13SQ; TP13SQ
SCK: TPTP13SQ; TP13SQ
SCL: TPTP13SQ; TP13SQ
SDA: TPTP13SQ; TP13SQ
SS: TPTP06R; TP06R
TH0: CON-MOLEX-2P-1.27MM048; 53048-02
TRG: SEEED-LED_SMD-LED-CLEAR-BLUE(0603)LED_0603; SEEED-LED_LED-0603
TXD: TPTP13SQ; TP13SQ
U1: ATMEGA48/88/168/328PA; 28M1
U4: LM2902QT; QFN16
⏚: TPTP13SQ; TP13SQ

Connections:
+5V: +5V.TP, C1.1, D8.2 (C), F1.2, R3.1, R8.1, TRG.+, U1.3 (VCC), U1.16 (AVCC), U4.2 (V+)
E0_1A: E0.2, J2.57 (63), J2.58 (64)
E0_1B: E0.1, J2.59 (65), J2.60 (66)
E0_2A: E0.3, J2.55 (61), J2.56 (62)
E0_2B: E0.4, J2.53 (59), J2.54 (60)
ERR_LED: ERR.+, U1.2 ((PCINT20/XCK/T0)_PD4)
FAN0_GATE: D5.-, FAN0.1, J2.29 (31)
FAN1_GATE: D4.-, FAN1.1, J2.30 (32)
GADJ_R0: R4.2 (1), R4.8 (2), U1.5 ((PCINT6/XTAL1/TOSC1)_PB6)
GADJ_R1: R4.3 (1), R4.7 (2), U1.6 ((PCINT7/XTAL2/TOSC2)_PB7)
GADJ_R2: R4.4 (1), R4.6 (2), U1.7 ((PCINT21/OC0B/T1)_PD5)
GADJ_R3: R4.5 (2), R9.2, U1.8 ((PCINT22/OC0A/AIN0)_PD6)
GAIN_FB: R2.1, R4.1, U4.13 (-IN)
GAIN_OUT: A-.TP, R1.2, R2.2, U4.14 (OUT), U4.16 (-IN)
GND: C1.2, C2.1, C3.2, C4.1, C5.1, C6.1, C7.1, C9.1, C11.1, C13.1, D1.P$1 (A), D8.1 (A), ERR.-, GND.TP, H1.B3,2, H2.B3,2, H3.B3,2, J2.13 (15), J2.14 (16), J2.31 (37), J2.32 (38), J2.51 (57), J2.52 (58), J2.S$1 (S), J2.S$2 (S), PWR.-, PZ1.2, R9.1, R14.1, R19.1, RDY.-, U1.4 (GND_2), U1.18 (GND), U1.29, U4.11 (V-), ⏚.TP
HE0-: D3.-, HE0.3, HE0.4, J2.15 (17), J2.16 (18), J2.17 (19), J2.18 (20), J2.19 (21), J2.20 (22), J2.21 (23), J2.22 (24)
LED_VCC: D3.+, D4.+, D5.+, R3.2
unnamed: PWR.+, R8.2
PT100+: C8.1, PT100.2, R7.2, R12.1
PT100-: C9.2, PT100.1, R11.2, R14.2
PT100_AMP+: C10.1, C12.2, R7.1, U4.4 (+IN)
PT100_AMP-: C11.2, C12.1, R11.1, U4.5 (-IN)
PT100_OUT: C13.2, J2.33 (39), R15.1
PT100_R: R15.2, U4.6 (OUT)
PZ+: D8.3 (AC), PZ1.1, PZ+.TP, R19.2, U4.12 (+IN)
PZ_AMP_OUT: R13.1, U4.15 (OUT)
RST: J2.38 (44), RST.TP, RST..TP, U1.25 (PC6_(RESET/PCINT14))
SCL: J2.41 (47), SCL.TP, U1.24 (PC5_(ADC5/SCL/PCINT13))
SDA: J2.42 (48), SDA.TP, U1.23 (PC4_(ADC4/SDA/PCINT12))
SPI_MISO: MISO.TP, U1.14 ((PCINT4/MISO)_PB4)
SPI_MOSI: MOSI.TP, U1.13 ((PCINT3/OC2A/MOSI)_PB3)
SPI_SCK: SCK.TP, U1.15 (PB5_(SCK/PCINT5))
SPI_SS: SS.TP, U1.12 ((PCINT2/SS/OC1B)_PB2)
TH0+: J2.27 (29), TH0.1
TH0-: J2.28 (30), TH0.2
TRG_LED: R6.2, RDY.+, TRG.-
TTL_RXD: J2.39 (45), RXD.TP, U1.26 (PD0_(RXD/PCINT16))
TTL_TXD: J2.40 (46), TXD.TP, U1.27 (PD1_(TXD/PCINT17))
VCC: HE0.1, HE0.2, J2.1 (3), J2.2 (4), J2.3 (5), J2.4 (6), J2.5 (7), J2.6 (8), J2.7 (9), J2.8 (10), J2.9 (11), J2.10 (12), J2.11 (13), J2.12 (14)
VCC_REG: 5V.TP, C2.2, C8.2, C10.2, D1.P$2 (C), F1.1, J2.36 (42), J2.37 (43), R12.2
VCOMP_PWM: R5.2, U1.11 ((PCINT1/OC1A)_PB1)
VCOMP_SENSE: A+.TP, C6.2, C7.2, R5.1, U1.20 (PC1_(ADC1/PCINT9)), U4.1 (+IN)
VREF_IN: C4.2, C5.2, R10.1, U4.9 (+IN)
V_FOL_PWM: R10.2, U1.1 ((PCINT19/OC2B/INT1)_PD3)
V_FOL_SENSE: R1.1, U1.19 (PC0_(ADC0/PCINT8)), U4.7 (OUT), U4.8 (-IN)
V_INT: C3.1, FAN0.2, FAN1.2, J2.23 (25), J2.24 (26), J2.25 (27), J2.26 (28)
X_1A: J2.47 (53), J2.48 (54)
X_1B: J2.49 (55), J2.50 (56)
X_2A: J2.45 (51), J2.46 (52)
X_2B: J2.43 (49), J2.44 (50)
X_MIN_TRIG: J2.34 (40)
Z_MIN_TRIG: J2.35 (41), R6.1, U1.9 ((PCINT23/AIN1)_PD7)
Z_TRG: INT.TP, R13.2, U1.28 (PD2_(INT0/PCINT18))

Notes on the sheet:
ATMega88/168/328
Power
LED's
Holes
Piezo Amp Circuit
Test Points
Connectors
VRef Buffer
Voltage Comparator DAC
Comparator
Piezo In
Amplifier Stage
8-bit PWM + LPF
- +
Gain Factor Adjust Ladder



Board: 2 copper layers, 42.6 x 46.5 mm, 71 parts (36 on the bottom side), 52 nets.

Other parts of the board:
U$1: LOGO-PYR0BALL-SS-20MM

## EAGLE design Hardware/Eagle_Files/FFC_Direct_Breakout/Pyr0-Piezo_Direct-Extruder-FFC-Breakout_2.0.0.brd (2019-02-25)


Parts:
5V, 12V: LEDCHIP-LED0805; CHIP-LED0805
C2: 100uf; ALU-C-D5.3MM_LEFT
C3, C4: 100uf; ALU-C-D5.3MM_RIGHT
C5: 10uF; CAPC2012X130
E0: C-GRID-04-70553; 70553-04
FAN0, FAN1: C-GRID-02-70553; 70553-02
H1, H2, H3, H4: HOLES_MOUNT-PAD-ROUND3.2; HOLES_3,2-PAD
HE0: KK-156-2
I2C: SEEED-CONNECTOR_DIP-BLACK-FEMALE-HEADER-VERT(4P-2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; HDRVR4W64P254_1X4_1016X254X575B
J1: FFC_MOLEX_0.5MM; FFC-60P_0.5_MOLEX_505110-6091
PWR: KK-156-2
Q2: 2N2907; TO92
R1: 240R; SEEED-RESISTOR_R0603
R2: 715R; SEEED-RESISTOR_R0603
R3: 2.05K; SEEED-RESISTOR_R0603
R4: 1K; SEEED-RESISTOR_R0603
R5: 0R; R0805
R6: 1R; R0805
R7: 10R; R0805
SW1: SEEED-SWITCH_DIP-TOGGLE-SWITCH-2CH-(2X3P-2.54)DPD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; SEEED-SWITCH_SW6-2.54-9.0X3.5X3.2+2.0MM
TH1: C-GRID-02-70553; 70553-02
U1: LM317DCY; SOT230P700X180-4N
U2: L78L05ACU; SOT89
UART: JST-2.54MM_5P-2.54JST_2.54MM_5P_F; HDRVR5W64P254_1X5_1270X254X575B
X_MIN: C-GRID-02-70553; 70553-02
X_MOT: C-GRID-04-70553; 70553-04
Z_MIN: C-GRID-02-70553; 70553-02

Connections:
5V_ADJ: R2.2, SW1.CH1A
5V_LED: 5V.A, SW1.CH2A
12V_ADJ: R3.2, SW1.CH1B
12V_LED: 12V.A, SW1.CH2B
+5V: C3.+, Q2.1 (C), R5.2, U2.1 (OUT)
AGND: 5V.C, 12V.C, C2.-, C3.-, C4.-, C5.1, H1.B3,2, H2.B3,2, H3.B3,2, H4.B3,2, I2C.2, J1.9 (11), J1.10 (12), J1.47 (53), J1.48 (54), J1.S$1 (S), J1.S$2 (S), PWR.1, R2.1, R3.1, U2.2 (GND), U2.PAD, UART.2, X_MIN.1, Z_MIN.1
BYP_GATE: Q2.2 (B), R7.2
E0_1A: E0.2, J1.3 (5), J1.4 (6)
E0_1B: E0.1, J1.1 (3), J1.2 (4)
E0_2A: E0.3, J1.5 (7), J1.6 (8)
E0_2B: E0.4, J1.7 (9), J1.8 (10)
FAN0_GATE: FAN0.1, J1.31 (37)
FAN1_GATE: FAN1.1, J1.32 (38)
HE0-: HE0.1, J1.39 (45), J1.40 (46), J1.41 (47), J1.42 (48), J1.43 (49), J1.44 (50), J1.45 (51), J1.46 (52)
LED_R: R4.2, SW1.COM2
LM317_VADJ: R1.1, SW1.COM1, U1.1 (ADJUST)
PT_100_OUT: J1.28 (30)
RST: J1.23 (25), UART.5
RXD: J1.22 (24), UART.4
SCL: I2C.4, J1.20 (22)
SDA: I2C.3, J1.19 (21)
TH0+: J1.33 (39), TH1.1
TH0-: J1.34 (40), TH1.2
TXD: J1.21 (23), UART.3
VCC: C2.+, FAN0.2, FAN1.2, HE0.2, J1.49 (55), J1.50 (56), J1.51 (57), J1.52 (58), J1.53 (59), J1.54 (60), J1.55 (61), J1.56 (62), J1.57 (63), J1.58 (64), J1.59 (65), J1.60 (66), PWR.2, Q2.3 (E), R6.1, U1.3 (INPUT)
VCC_REG: I2C.1, J1.24 (26), J1.25 (27), R5.1, UART.1
VREG_IN: R6.2, R7.1, U2.3 (IN)
V_INT: C4.+, C5.2, J1.35 (41), J1.36 (42), J1.37 (43), J1.38 (44), R1.2, R4.1, U1.4 (OUTPUT)
X_1A: J1.13 (15), J1.14 (16), X_MOT.2
X_1B: J1.11 (13), J1.12 (14), X_MOT.1
X_2A: J1.15 (17), J1.16 (18), X_MOT.3
X_2B: J1.17 (19), J1.18 (20), X_MOT.4
X_MIN_TRIG: J1.27 (29), X_MIN.2
Z_MIN_TRIG: J1.26 (28), Z_MIN.2

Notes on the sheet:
5V / 12V Switchable Fan Supply
5V Ripple Rejected AVR/Piezo Supply


Board: 2 copper layers, 64.8 x 63.9 mm, 34 parts (0 on the bottom side), 33 nets.

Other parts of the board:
U$1: LOGO-PYR0BALL

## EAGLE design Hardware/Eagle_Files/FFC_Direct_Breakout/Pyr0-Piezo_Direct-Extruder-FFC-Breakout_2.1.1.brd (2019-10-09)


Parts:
5V, 12V: LEDCHIP-LED0805; CHIP-LED0805
C2: 100uf; ALU-C-D5.3MM_LEFT
C3, C4: 100uf; ALU-C-D5.3MM_RIGHT
C5: 10uF; CAPC2012X130
D1, D2, D3, D4, D5, D6, D7, D8, D9, D10, D11, D12, D13, D14, D15, D16: DIODE_SCHOTTKY_SINGLE; DO-214AC
E0: C-GRID-04-70553; 70553-04
FAN0, FAN1: C-GRID-02-70553; 70553-02
H1, H2, H3, H4: HOLES_MOUNT-PAD-ROUND3.2; HOLES_3,2-PAD
HE0: KK-156-2
I2C: SEEED-CONNECTOR_DIP-BLACK-FEMALE-HEADER-VERT(4P-2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; HDRVR4W64P254_1X4_1016X254X575B
J2: FFC-15P-1MM
PT100: C-GRID-02-70543; 70543-02
PWR: KK-156-2
Q2: MMBT2907ALT1-PNP-SOT23-BEC; SOT23-BEC
R1: 240R; SEEED-RESISTOR_R0603
R2: 715R; SEEED-RESISTOR_R0603
R3: 2.05K; SEEED-RESISTOR_R0603
R4: 1K; SEEED-RESISTOR_R0603
R5: 0R; R0805
R6: 1R; R0805
R7: 10R; R0805
SW1: SEEED-SWITCH_DIP-TOGGLE-SWITCH-2CH-(2X3P-2.54)DPD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; SEEED-SWITCH_SW6-2.54-9.0X3.5X3.2+2.0MM
TH1: C-GRID-02-70553; 70553-02
U1: LM317DCY; SOT230P700X180-4N
U2: L78L05ACU; SOT89
UART: JST-2.54MM_5P-2.54JST_2.54MM_5P_F; HDRVR5W64P254_1X5_1270X254X575B
X1: FFC-40P-0.5SH; FH12-40S-0.5SH
X_MIN: C-GRID-02-70553; 70553-02
X_MOT: C-GRID-04-70553; 70553-04
Z_MIN: C-GRID-02-70553; 70553-02

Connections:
5V_ADJ: R2.2, SW1.CH1A
5V_LED: 5V.A, SW1.CH2A
12V_ADJ: R3.2, SW1.CH1B
12V_LED: 12V.A, SW1.CH2B
+5V: C3.+, Q2.C, R5.2, U2.1 (OUT)
AGND: 5V.C, 12V.C, C2.-, C3.-, C4.-, C5.1, D1.A, D3.A, D5.A, D7.A, D9.A, D11.A, D13.A, D15.A, H1.B3,2, H2.B3,2, H3.B3,2, H4.B3,2, I2C.2, J2.P$1, J2.P$4, J2.P$9, J2.P$16 (TP), J2.P$17 (TP), PT100.1, PWR.1, R2.1, R3.1, U2.2 (GND), U2.PAD, UART.2, X1.1, X1.2, X1.3, X1.4, X1.5, X1.6, X1.7, X1.31, X1.32, X_MIN.1, Z_MIN.1
BYP_GATE: Q2.B, R7.2
E0_1A: D13.C, D14.A, E0.2, X1.37, X1.38
E0_1B: D15.C, D16.A, E0.1, X1.39, X1.40
E0_2A: D11.C, D12.A, E0.3, X1.35, X1.36
E0_2B: D9.C, D10.A, E0.4, X1.33, X1.34
FAN0_GATE: FAN0.1, X1.11
FAN1_GATE: FAN1.1, X1.10
HE0-: HE0.1, J2.P$5, J2.P$6, J2.P$7, J2.P$8
LED_R: R4.2, SW1.COM2
LM317_VADJ: R1.1, SW1.COM1, U1.1 (ADJUST)
PT_100_OUT: PT100.2, X1.12, X1.13
RST: UART.5, X1.18
RXD: UART.4, X1.19
SCL: I2C.4, X1.21
SDA: I2C.3, X1.22
TH0+: TH1.1, X1.9
TH0-: TH1.2, X1.8
TXD: UART.3, X1.20
VCC: C2.+, D2.C, D4.C, D6.C, D8.C, D10.C, D12.C, D14.C, D16.C, FAN0.2, FAN1.2, HE0.2, J2.P$10, J2.P$11, J2.P$12, J2.P$13, J2.P$14, J2.P$15, PWR.2, Q2.E, R6.1, U1.3 (INPUT)
VCC_REG: I2C.1, R5.1, UART.1, X1.16, X1.17
VREG_IN: R6.2, R7.1, U2.3 (IN)
V_INT: C4.+, C5.2, J2.P$2, J2.P$3, R1.2, R4.1, U1.4 (OUTPUT)
X_1A: D5.C, D6.A, X1.27, X1.28, X_MOT.2
X_1B: D7.C, D8.A, X1.29, X1.30, X_MOT.1
X_2A: D3.C, D4.A, X1.25, X1.26, X_MOT.3
X_2B: D1.C, D2.A, X1.23, X1.24, X_MOT.4
X_MIN_TRIG: X1.14, X_MIN.2
Z_MIN_TRIG: X1.15, Z_MIN.2

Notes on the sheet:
5V / 12V Switchable Fan Supply
5V Ripple Rejected AVR/Piezo Supply



Board: 2 copper layers, 64.8 x 63.9 mm, 52 parts (17 on the bottom side), 34 nets.

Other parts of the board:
U$1: LOGO-PYR0BALL

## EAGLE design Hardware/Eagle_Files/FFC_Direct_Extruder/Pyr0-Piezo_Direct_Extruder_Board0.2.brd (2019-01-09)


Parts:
5V: TPTP06R; TP06R
+5V: TPTP13SQ; TP13SQ
C1, C2, C3: 1uF; CAPC1609X80
D1, D6: BAV199; SOT23
D2, D3, D4, D5: SEEED-LED_SMD-LED-CLEAR-BLUE(0603)LED_0603; SEEED-LED_LED-0603
E0: C-GRID-04-70553; 70553-04
FAN0, FAN1: CON-MOLEX-2P-1.27MM048; 53048-02
GND: TPTP13SQ; TP13SQ
H1, H2, H3: HOLES_MOUNT-PAD-ROUND2.8; HOLES_2,8-PAD
HE0: JST-2.54-2X2JST-DUPONT-2.54-2X2; HDRRAR4W64P254_2X2_556X736X556B
INT: TPTP06R; TP06R
J1: SFW24R-1STE1LF; CON24_1X24_DRB_SFW
MISO: TPTP06R; TP06R
MOSI: TPTP06R; TP06R
PWR: SEEED-LED_SMD-LED-CLEAR-BLUE(0603)LED_0603; SEEED-LED_LED-0603
PZ1: CON-MOLEX-2P-1.27MM048; 53048-02
Q1: 2PC4081-NPN; SC70
R1: 1M; R0402
R2: 47K; R0402
R3, R6, R8: SMD-RES-0R-5%-1/16W(0402); R0402
R4: 220; R0402
R5: 1K; R0402
R7: 330; R0402
RST: TPTP06R; TP06R
RST.: TPTP13SQ; TP13SQ
RXD: TPTP13SQ; TP13SQ
SCK: TPTP06R; TP06R
SCL: TPTP13SQ; TP13SQ
SDA: TPTP13SQ; TP13SQ
SS: TPTP06R; TP06R
TH0: CON-MOLEX-2P-1.27MM048; 53048-02
TRG: SEEED-LED_SMD-LED-CLEAR-BLUE(0603)LED_0603; SEEED-LED_LED-0603
TXD: TPTP13SQ; TP13SQ
U1: ATMEGA48PA-MMHR28M1-L; 28M1-L
U2: L78L05ACU; SOT89
U3: MCP6001T-I/OTSOT-23-5_MC-L; SOT-23-5_MC-L
VR1: TC33X-2-103E; TRIM_TC33X-2-103E

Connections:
5V_DC: 5V.TP, +5V.TP, C1.2, D6.2 (C), R3.1, R8.1, U1.3 (VCC), U1.16 (AVCC), U2.1 (OUT), U3.5 (VDD), VR1.2
AMP_IN+: PZ1.1, U3.3 (VIN+)
E0_1A: E0.3, J1.5 (55), J1.6 (66)
E0_1B: E0.4, J1.7 (77), J1.8 (88)
E0_2A: E0.2, J1.3 (33), J1.4 (44)
E0_2B: E0.1, J1.1 (11), J1.2 (22)
FAN0_GATE: D5.-, FAN0.1, J1.17 (1717)
FAN1_GATE: D4.-, FAN1.1, J1.15 (1515)
GND: C1.1, C2.1, C3.2, D1.1 (A), D2.-, D6.3 (AC), GND.TP, H1.B2,8, H2.B2,8, H3.B2,8, J1.12 (1212), J1.14 (1414), J1.16 (1616), J1.18 (1818), J1.25 (2525), J1.26 (2626), PWR.-, PZ1.2, Q1.2 (E), R2.1, R4.1, TRG.-, U1.4 (GND_2), U1.18 (GND), U1.29, U2.2 (GND), U2.PAD, U3.2 (VSS)
HE0-: D3.-, HE0.3, HE0.4, J1.21 (2121), J1.22 (2222)
LED_VCC: D3.+, D4.+, D5.+, R3.2
unnamed: INT.TP, U1.28 (PD2_(INT0/PCINT18))
unnamed: PWR.+, R8.2
unnamed: R5.2, U3.4 (VIN-)
PZ_IN+: R5.1, R7.2, U3.1 (VOUT)
RST: RST.TP, RST..TP, U1.25 (PC6_(RESET/PCINT14))
SCL: SCL.TP, U1.24 (PC5_(ADC5/SCL/PCINT13))
SDA: SDA.TP, U1.23 (PC4_(ADC4/SDA/PCINT12))
SPI_MISO: MISO.TP, U1.14 ((PCINT4/MISO)_PB4)
SPI_MOSI: MOSI.TP, U1.13 ((PCINT3/OC2A/MOSI)_PB3)
SPI_SCK: SCK.TP, U1.15 (PB5_(SCK/PCINT5))
SPI_SS: SS.TP, U1.12 ((PCINT2/SS/OC1B)_PB2)
TH0+: J1.20 (2020), TH0.1
TH0-: J1.19 (1919), TH0.2
TRG_LED: D2.+, R6.2, TRG.+
TTL_RXD: RXD.TP, U1.26 (PD0_(RXD/PCINT16))
TTL_TXD: TXD.TP, U1.27 (PD1_(TXD/PCINT17))
T_POT_IN: R2.2, U1.21 (PC2_(ADC2/PCINT10)), VR1.1
T_TRG_BASE: Q1.1 (B), R4.2, R7.1
VCC: HE0.1, HE0.2, J1.23 (2323), J1.24 (2424)
VCC_REG: C2.2, D1.3 (AC), J1.9 (99), U2.3 (IN)
V_INT: C3.1, FAN0.2, FAN1.2, J1.10 (1010), J1.11 (1111)
Z_MIN_TRIG: J1.13 (1313), R6.1, U1.11 ((PCINT1/OC1A)_PB1)
Z_TRG: Q1.3 (C), U1.19 (PC0_(ADC0/PCINT8))



Board: 2 copper layers, 38.1 x 46.5 mm, 49 parts (14 on the bottom side), 34 nets.

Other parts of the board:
U$1: LOGO-PYR0BALL-SS-20MM

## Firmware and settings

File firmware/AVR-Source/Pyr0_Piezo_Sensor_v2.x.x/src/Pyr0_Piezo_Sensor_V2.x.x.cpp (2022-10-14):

/*
  Piezoelectric Z-Axis sensor using AtMega88/168/328 (AtMega 48 doesnt have enough memory for this version)

  This sketch reads a piezo element to detect a touch of the printer's nozzle to the bed.
  The sense pin is tied to an interrupt, which is pulled high by internal pullup resistor.
  When the piezo touches the bed, the amplification circuit will draw the interrupt pin low
  and the atmega will output a pulse based on the programmed trigger duration

 * PD2 INT0 (Piezo In 'D2')
 * D7 PCINT23 (Trigger OUT 'D7')
 * PC0 ADC0 (Voltage Reference Check 'A0')
 * PC1 ADC1 (Sensitivity Adjustment Check 'A1')
 * PD4 PCINT20 (Error feedback LED 'D4')
 * PB6 PCINT6 (Gain Adjustment Resistor 0 'D20')
 * PB7 PCINT7 (Gain Adjustment Resistor 1 'D21')
 * PD5 T1 (Gain Adjustment Resistor 2 'D5')
 * PD6 PCINT22 (Gain Adjustment Resistor 3 'D6')
 * PB0 PCINT0 (VCC Adjustment Resistors 'D8')
 * PB1 OC1A (Comparator VRef PWM Out 'D9')
 * PD3 OC2B (Voltage Follower VRef PWM Out 'D3')

  Schematics for this project can be found here: https://github.com/pyr0ball/pyr0piezo/tree/master/docs/Schematics

  For Arduino IDE use MCUdude MiniCore: https://mcudude.github.io/MiniCore/package_MCUdude_MiniCore_index.json


  created 2/18/2019
  by Alan "pyr0ball" Weinstock

  This code is in the public domain.
------------------------------------------------------------*/

/*-----------------------------------------------------------
To set the below parameters using serial input, use the following:

To change trigger active duration: TRG_D [integer for milliseconds]
To change gain factor: GAIN_F [integer for gain state - see note*]
To change the output logic: LOGIC [0|1] (0 for active low, 1 for active high)
To enable piezo plugged detection: PZDET [0|1] (0 for disabled, 1 for enabled)
To set the sensor's output voltage: VCCSW [0|1] (0 for 3.3v, 1 for 5v)
To change ADC hysteresis value: HYST [integer in millivolts]
To change sensor input pullup vRef low threshold: VFOL [integer in millivolts]
To change comparator trigger high threshold: VCOMP [integer in millivolts]
To change the duration between ADC measurements: LOOP_D [integer in milliseconds]
To update the internal vRef constant value **(see notes below): CONST [long value]

You can also enable or disable DEBUG output with: DEBUG [0|1]

You can query the current configuration with: CONFIG
You can query the current state (including ADC measurements) with: STATE

To set all settings to defaults, use: ERASE

These commands should be wrapped in this format:
CMD INT

Examples:
GAIN_F 3 <~ set gain factor to index 3 (6x)
VFOL 2350 <~ set the vref floor to 2.35V
DEBUG 1 <~ Enable debug output
STATE <~ display current sensor status

*Note for Gain Factor:
The gain STATE is representative of these values:
0 = 3x
1 = 3.5x
2 = 4.33x
3 = 6x
4 = 11x

**Note for calibrating internal 1.1v vRef:
The ADC reading function assumes an "ideal" multiplier constant. Each Atmega
chip is slightly different, so it won't be completely accurate without tuning.
Most of the time this won't be necessary, so don't mess with this if you don't
know what you're doing!
The reading can be fine-tuned by using a multimeter, and this equation:

scale_constant = internal1.1Ref * 1023 * 1000

where

internal1.1Ref = 1.1 * Vcc1 (per voltmeter) / Vcc2 (per readVcc() function)

If the scale_constant calculated is different from the default 1125300,
update the voltMeterConstant variable in pP_config.h with the correct value

------------------------------------------------------------*/

// i2c input toggle. Uncomment to enable
#define I2C_INPUT

// Headers, variables, and functions
#include "LightChrono.h"
#include "pP_function.h"
#include "pP_i2c.hpp"
#include "pP_pins.h"
#include "pP_serial.h"
#include "pP_volatile.h"
#include <Arduino.h>

void setup() {
  // Setup PWM on voltage follower (PD3)
  TCCR2A = (1 << COM2B1) | (0 << COM2B0) | (0 << WGM21) | (1 << WGM20);
  TCCR2B = (0 << WGM22) | (0 << CS22) | (0 << CS21) | (1 << CS20);
  DDRD |= (1 << DDD3);

  // Setup PWM on comparator (PB1)
  TCCR1A = (1 << COM1A1) | (0 << COM1A0) | (1 << WGM11) | (1 << WGM10);
  TCCR1B = (0 << WGM13) | (0 << WGM12) | (0 << CS12) | (0 << CS11) | (1 << CS10);
  DDRB |= (1 << DDB1);

  pinMode(TRG_OUT, OUTPUT); // declare the Trigger as as OUTPUT
  pinMode(ERR_LED, OUTPUT);
  pinMode(PZDET_PIN, INPUT_PULLUP);
  pinMode(Z_TRG, INPUT_PULLUP); // declare z-sense input with pullup
  pinMode(V_FOLLOW_PIN, INPUT);
  pinMode(VCOMP_SENSE_PIN, INPUT);
  pinMode(GADJ_R0, INPUT); // declare input to set high impedance
  pinMode(GADJ_R1, INPUT); // declare input to set high impedance
  pinMode(GADJ_R2, INPUT); // declare input to set high impedance
  pinMode(GADJ_R3, INPUT); // declare input to set high impedance

  attachInterrupt(digitalPinToInterrupt(Z_TRG), pulse, FALLING);

  Serial.begin(9600);
  Serial.print("Pyr0-Piezo Z-Probe Firmware ");
  Serial.println(PP_VERSION);
  Serial.println("Info: https://docs.pyroballpcbs.com");
  Serial.println("Source: https://github.com/pyr0ball/pyr0piezo");
  Serial.println("Initializing Pyr0-Piezo Sensor...");

  i2cInit();

  restoreConfig();

  adjustGain();

  adjustVcc();

  digitalWriteFast(TRG_OUT, !LOGIC);
}

/*------------------------------------------------*/

void loop() {
  if (mainLoop.hasPassed(LOOP_DUR)) {
    mainLoop.restart();

    // Get Serial Input
    serialInput();

    // Set any new parameters from serial input
    if (serialIncoming) {
      updateParams();
    }

    // Set the amplification gain factor
    adjustGain();

    // Set the VCC input switch
    adjustVcc();

    // Check voltage of first and second stages and compare against thresholds
    readVin();
    VComp = analogReadFast(VCOMP_SENSE_PIN);
    VFol = analogReadFast(V_FOLLOW_PIN);

    VLast = VOld - Vin;
    if (VLast > Hyst || VLast < -Hyst) {
      // Voltage Follower adjustment
      adjustFollow();
      // Voltage Comparator adjustment
      adjustComp();
      // Alert the user that auto-calibration is ongoing
      ERR_STATE = 1;
    } else {
      ERR_STATE = 0;
    }

    // Check that the piezo disk is properly connected
    pzConCheck();

    // Print state if debug is on
    if (Debug > 0) {
      serialPrintState();
    }
  }

  // Blink LED
  if (blinkLoop.hasPassed(BLINK_DURATION) && BlinkCount > 0) {
    blinkLoop.restart();
    BlinkCount--;
    digitalWriteFast(ERR_LED, BlinkCount % 2);
  }

  if (lastTriggerTimestamp > 0 && millis() - lastTriggerTimestamp > TRG_DUR) {
    digitalWriteFast(TRG_OUT, !LOGIC);
    lastTriggerTimestamp = 0;
  }
}

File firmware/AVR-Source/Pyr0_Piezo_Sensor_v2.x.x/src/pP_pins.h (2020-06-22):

/* pyr0-piezo pins configuration file

Default pins (based on Rev.2.x.xPCB layout)

 * PD2 INT0 (Piezo In 'D2')
 * D7 PCINT23 (Trigger OUT 'D7')
 * PC0 ADC0 (Voltage Reference Check 'A0')
 * PC1 ADC1 (Sensitivity Adjustment Check 'A1')
 * PD4 PCINT20 (Error feedback LED 'D4')
 * PB6 PCINT6 (Voltage Adjustment Resistor 0 'D20')
 * PB7 PCINT7 (Voltage Adjustment Resistor 1 'D21')
 * PD5 T1 (Voltage Adjustment Resistor 2 'D5')
 * PD6 PCINT22 (Voltage Adjustment Resistor 3 'D6')
 * PB1 OC1A (Comparator VRef PWM Out 'D9')
 * PD3 OC2B (Voltage Follower VRef PWM Out 'D3')
*/

#ifdef __AVR_ATmega328PB__ // Pin assignments for 328PB variant

// Analog Pin Assignments
#define V_FOLLOW_PIN A0    // Sense pin to check Voltage Follower stage
#define VCOMP_SENSE_PIN A1 // Sense pin to check comparator stage voltage

// Digital Pin Assignments
#define TRG_OUT 7 // LED and Z-Min trigger output connected to digital pin 7
//#define TRG_OUT 13      // For testing on Atmega328/2560, Output is moved to onboard LED pin
#define Z_TRG 2      // the piezo is connected to INT0 / digital pin 2
#define ERR_LED 4    // LED will blink if optimal voltage range cannot be achieved
#define GADJ_R0 20   // Auto-adjust ladder pin assignments
#define GADJ_R1 21   // "
#define GADJ_R2 5    // "
#define GADJ_R3 6    // "
#define V_FOL_PWM 3  // PWM analog output pin for voltage follower adjustment
#define VCOMP_PWM 9  // PWM analog output pin for comparator adjustment
#define PZDET_PIN 16 // Digital input pin for detecting piezo connection
#define VCCSW_PIN 8  // VCC variable regulator switch pin

#endif //__AVR_ATmega328PB__

#ifdef __AVR_ATmega328P__ // Pin assignments for 328P variant

// Analog Pin Assignments
#define V_FOLLOW_PIN A0    // PC0 Sense pin to check Voltage Follower stage
#define VCOMP_SENSE_PIN A1 // PC1 Sense pin to check comparator stage voltage

// Digital Pin Assignments
#define TRG_OUT 7 // LED and Z-Min trigger output connected to digital pin 7
//#define TRG_OUT 13      // For testing on Atmega328/2560, Output is moved to onboard LED pin
#define Z_TRG 2      // the piezo is connected to INT0 / digital pin 2
#define ERR_LED 4    // LED will blink if optimal voltage range cannot be achieved
#define GADJ_R0 20   // PB6 Auto-adjust ladder pin assignments
#define GADJ_R1 21   // PB7 "
#define GADJ_R2 5    // PD5 "
#define GADJ_R3 6    // PD6 "
#define V_FOL_PWM 3  // PD3 PWM analog output pin for voltage follower adjustment
#define VCOMP_PWM 9  // PB1 PWM analog output pin for comparator adjustment
#define PZDET_PIN 16 // PC2 Digital input pin for detecting piezo connection
#define VCCSW_PIN 8  // PB0 VCC variable regulator switch pin

#endif //__AVR_ATmega328P__

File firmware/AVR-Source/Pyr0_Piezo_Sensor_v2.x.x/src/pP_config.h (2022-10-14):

#ifndef PP_CONFIG_H
#define PP_CONFIG_H

#include "stdint.h"

// Configurable settings:

#define GAIN_FACTOR_DEFAULT 2 // Gain adjustment factor. 0=3x, 1=3.5x, 2=4.33x, 3=6x, 4=11x
#define GAIN_FACTOR_ADDRESS 0
extern int GAIN_FACTOR;

#define FOLLOWER_THRESHOLD_DEFAULT 1450 // Voltage follower default voltage in mV
#define FOLLOWER_THRESHOLD_ADDRESS 4
extern int followerThrs;

#define COMP_THRESHOLD_DEFAULT 2850 // Comparatore Vref default voltage in mV
#define COMP_THRESHOLD_ADDRESS 8
extern int compThrs;

#ifndef InitCount
#define InitCount 6 // Number of times to blink the LED on start
#endif

#define LOOP_DUR_DEFAULT 50 // duration of time between ADC checks and other loop functions
#define LOOP_DUR_ADDRESS 12
extern int LOOP_DUR;

#define TRG_DUR_DEFAULT 20 // duration of the Z-axis pulse sent, in ms
#define TRG_DUR_ADDRESS 16
extern int TRG_DUR;

#define HYST_DEFAULT 20
#define HYST_ADDRESS 20
extern int Hyst; // Hysteresis value for ADC measurements

#define LOGIC_DEFAULT 0
#define LOGIC_ADDRESS 22
extern int LOGIC; // Trigger logic scheme, Active LOW is default

#define PZDET_DEFAULT 0
#define PZDET_ADDRESS 26
extern int PZDET; // Enable or disable piezo connection detection, default is off

#define VCCSW_DEFAULT 1
#define VCCSW_ADDRESS 28
extern int VCCSW; // Set the signal output to 3.3v [0] or 5v logic [1]

extern int Debug;

#define VM_CONST_ADDRESS 30
#define VM_CONST_DEFAULT 1125300L
extern long voltMeterConstant; // For fine tuning input voltage sense

#define I2C_SLAVE_ADDRESS 24
extern uint8_t pP_i2c_address;

#ifndef PP_VERSION
    #define PP_VERSION "2.3.2"
#endif // PP_VERSION fallback if python script fails

#define BLINK_DURATION 100

void eraseEEPROM();
void setDefaultConfig();
void restoreConfig();

#endif // PP_CONFIG_H

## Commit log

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2019-01-09 Removed debug serial output, fixed voltage reference divisor
2019-01-09 Fixed syntax error in voltage adjustment function
    Addresses broken code in https://github.com/pyr0ball/pyr0piezo/issues/1
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2019-01-09 Moved test points for spi to ICSP standard header
    [Extruder_Board1.2.brd, Extruder_Board1.2.sch]
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2019-01-10 Fixed accidental short of pin to ground
    [Extruder_Board1.2.brd, Extruder_Board1.2.sch]
2019-01-10 Adjusted trace placement, added logo to bottom of board
    [Extruder_Board_programmer.brd]
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2019-01-15 fixed trace accidentally connected to ground
    [Extruder_Board1.2.brd, Extruder_Board1.2.sch, PiezoStandalone1.0.brd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]
2019-01-21 Renamed boards, Fixed programmer
    - Renamed boards to more closely match change in spec/design revision
    - Added required components to usb serial board stack
    - Fixes https://github.com/pyr0ball/pyr0piezo/issues/9
    - Minor change to voltage values to stay consistent with local tests
    [AVR_Board_programmer.brd, AVR_Board_programmer.sch, AVR_Board_programmer_BOM.csv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]
2019-01-23 Rebuilt and corrected mount hole spacing
    Partially addresses https://github.com/pyr0ball/pyr0piezo/issues/10
    [Fulcrum_20mm.stl]
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2019-01-25 Created tolerance cavities for inserting bearings
    Addresses https://github.com/pyr0ball/pyr0piezo/issues/11
    Added cavity to rear middle of channel, and cutout on sides to allow
    for easier insertion into the mount. Ziptie location should keep the
    bearing stable even with cavity
2019-01-25 Added tolerance for knurled nut insert
    Also removed duplicate model
    [Creality-Piezo-Board Mount.stl, Creality-Piezo-Nozzle-Mount.stl]
2019-01-25 Added cutout for slide-on nozzle mount to be easily added
    [Creality-Piezo-Plate-Mount.stl]
2019-01-26 Added ICSP Header/breakout to programmer
    Also added secondary footprint for alternate TVS Diode
    (ESD protection component) that's about 1/10th the cost
    of the one currently used (suggested by the UART Bridge's
    Datasheet.
    [AVR_Board_programmer.brd, AVR_Board_programmer.sch]
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2019-01-26 re-adding files after fix-merge
    [AVR_Board_programmer.brd, AVR_Board_programmer.sch]
2019-01-26 Replaced opamps with single quad-channel
    Replacement has better specs and is not backordered. BOM price is also a
    bit better.
    [PiezoStandalone1.1.brd, PiezoStandalone1.1.sch]
2019-01-31 Fixed airwires and overlaps caused by swapping IC
    Reminder to always do a DRC after changin BOM!
    [AVR_Board_programmer.brd, AVR_Board_programmer.sch]
2019-01-31 re-adding AVR programmer after fixing conflict
    [AVR_Board_programmer.brd, AVR_Board_programmer.sch]
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2019-02-04 updated with minor fixes to text placement
    [PiezoStandalone1.0.1.brd, PiezoStandalone1.0.1.sch]
2019-02-05 fixed missing ziptie channels on prusa mount
2019-02-07 moved usb to bottom of board, fixed caps
    Decoupling capacitors were connected on
    the wrong voltage regulation input
    [AVR_Board_programmer1.0.1.brd, AVR_Board_programmer1.0.1.sch]
2019-02-07 v1.1 Piezo Standalone board
    - Added overvolt/overcurrent protection
    via zener diode and fuse
    - Swapped LM358 dual channel opamp + MCP6001 Single Channel opamp for LM2902 Quad Channel.
    - Added jumper to bypass Vreg for < 6V input
    [PiezoStandalone1.1.brd, PiezoStandalone1.1.sch]
2019-02-07 Added missing 0.1uF cap on AVR Vcc
    [PiezoStandalone1.1.brd, PiezoStandalone1.1.sch]
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2019-02-08 fixed footprint for LM2902, optimized traces
    [PiezoStandalone1.1.brd, PiezoStandalone1.1.sch]
2019-02-08 Added version with PT100 amp integrated
    - utilizes the 4th unused channel on LM2902
    - added additional conductor on controller connector
    - fixed passive label locations
    [PiezoStandalone_PT100_1.1.1.brd, PiezoStandalone_PT100_1.1.1.sch]
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2019-02-08 Fixed airwires and overlaps
    [PiezoStandalone_PT100_1.1.1.brd, PiezoStandalone_PT100_1.1.1.sch]
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2019-02-10 Fixed spacing for zener diode
    [PiezoStandalone_PT100_1.1.1.brd, PiezoStandalone_PT100_1.1.1.sch]
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2019-02-11 Added support channels for upper bearings
    Hopefully will address bearing alignment and prevent binding
    addresses issue https://github.com/pyr0ball/pyr0piezo/issues/11
2019-02-11 Added v2.0.0 Extruder board, rewire for 60p
    This is a first draft of the new rewiring scheme
    Moving from 1mm pitch 26pin to 0.5mm pitch 60pin
    for greater number of signals. Should allow for
    the new planned features.
    [Extruder_Board2.0.0.brd, Extruder_Board2.0.0.sch]
2019-02-11 Gave some extra space to zener diode
    related to https://github.com/pyr0ball/pyr0piezo/issues/12
    [PiezoStandalone_PT100_1.1.1.brd]
2019-02-11 Added drawing for Standalone board component layout
    Should be viable as a first step in creating an assembly
    guide. Relates to https://github.com/pyr0ball/pyr0piezo/issues/14
2019-02-12 Brought FFC extruder board up to v1.1 spec
    Swapped opamps for LM2902 quad-channel
    [Extruder_Board1.1.0.brd, Extruder_Board1.1.0.sch]
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2019-02-13 Modified footprints and added 3D Models for caps
    [Direct-Extruder-FFC-Breakout_1.0.0.brd, Direct-Extruder-FFC-Breakout_1.0.0.sch]
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2019-02-15 fixed some spacing and labelling
    [Extruder_Board1.1.0.brd, Extruder_Board1.1.0.sch]
2019-02-15 Rev.2.0.0 - Rewired for full piezo circuit control
    - Moved ERR_LED to Pin2/PD4; replaced with V_FOL_PWM on Pin1/OC2B to
    adjust Voltage Follower level
    - Moved Z_Min_Trig to Pin9/PD7; replaced with VCOMP_PWM for adjusting
    comparator threshold voltage reference
    - Attached series resistor ladder to gain amp voltage divider,changed
    all resistor values to 470R, allowing a gain of 5 values: 10x, 6.8x,
    5.15x, 4.15x, and 3.47x
    - Repositioned decoupling capacitors to be more in line with the
    schematic
    [PiezoStandalone_PT100_2.0.0.brd, PiezoStandalone_PT100_2.0.0.sch]
2019-02-15 Corrected naming convention for Standalone 1.0.2
    [PiezoStandalone1.0.2.brd, PiezoStandalone1.0.2.sch]
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2019-02-18 Moved schematics to correct documentation folder
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2019-02-18 Swapped/repositioned components
    - Swapped individual 0402 resistors for 4x array. related to https://github.com/pyr0ball/pyr0piezo/issues/16
    - repositioned LPF capacitors for easier installation. related to https://github.com/pyr0ball/pyr0piezo/issues/15
    [PiezoStandalone_PT100_2.0.0.brd, PiezoStandalone_PT100_2.0.0.sch]
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2019-02-21 fixed pin assignment from debug edit
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2019-02-24 Updated schematic with cleaned up and labelled circuit
    [PiezoStandalone_PT100_2.0.0.sch]
2019-02-25 Brought FFC board up to v2.x spec.
    Still ToDo: route traces for PT100 input to amp
    [Extruder_Board2.0.0.brd, Extruder_Board2.0.0.sch]
2019-02-25 Removed cavity behind bearings causing binding
2019-02-25 Added X-motor and X-min breakouts
    Added in preparation for https://github.com/pyr0ball/pyr0piezo/issues/18
    [Direct-Extruder-FFC-Breakout_2.0.0.brd, Direct-Extruder-FFC-Breakout_2.0.0.sch]
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2019-02-25 Started Creality X-axis extruder breakout board
    Started https://github.com/pyr0ball/pyr0piezo/issues/18
    [Pyr0-Piezo-FFC-Creality-X-Board.brd, Pyr0-Piezo-FFC-Creality-X-Board.sch]
2019-02-25 Added pin assignments for serial/i2c comms on FFC
    Builds necessary back-channel for https://github.com/pyr0ball/pyr0piezo/issues/2
    Also added pin assignments used in https://github.com/pyr0ball/pyr0piezo/issues/18
    [Extruder_Board2.0.0.brd, Extruder_Board2.0.0.sch]
2019-02-25 Added schematic for wiring up UART for programming
    Addition to https://github.com/pyr0ball/pyr0piezo/issues/14
    [USB-UART-Wiring-Example.sch]
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2019-02-26 Finished first iteration of x-gantry board
    First version to address https://github.com/pyr0ball/pyr0piezo/issues/18
    [PiezoStandalone_PT100_2.0.0.sch, Pyr0-Piezo-FFC-Creality-X-Board.2.0.0.brd, Pyr0-Piezo-FFC-Creality-X-Board.2.0.0.sch]
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2019-03-08 Fixed PWM output syntax
    Fixes issue https://github.com/pyr0ball/pyr0piezo/issues/19
    [Pyr0_Piezo_Sensor_v2.x.x.ino]
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2019-03-09 Switched to 32VQFN package Atmega328pa
    Added pins to input header for I2C, removed test pads, in prep for https://github.com/pyr0ball/pyr0piezo/issues/22
    Repositioned components, optimized trace routing
    [PiezoStandalone_AVR_3.0.0.brd, PiezoStandalone_AVR_3.0.0.sch]
2019-03-09 Swapped Atmega for ATSAMD21E family MCU
    Started work on https://github.com/pyr0ball/pyr0piezo/issues/21
    Started work on https://github.com/pyr0ball/pyr0piezo/issues/22
    Started pin assignments and board mapping for ARM MCU
    Added i2c pins to input header
    [PiezoStandalone_3.0.0.brd, PiezoStandalone_3.0.0.sch]
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2019-03-13 Standardized naming conventions, organized
    Moved each set of board files to individual folders
    [AVR_Board_programmer_BOM.csv, Pyr0-Piezo-AVR_Board_programmer_0.1.brd, Pyr0-Piezo-AVR_Board_programmer_0.1.sch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]
2019-03-13 Swapped pins for 2-pin headers to match standard
    [Pyr0-Piezo-Standalone_2.0.1.brd, Pyr0-Piezo-Standalone_2.0.1.sch]
2019-03-14 Replaced serial parser, verified parameters update
    Progress on https://github.com/pyr0ball/pyr0piezo/issues/2
    See notes on wiki for serial input format
    [Pyr0_Piezo_Sensor_v2.x.x.ino]
2019-03-16 Added rudimentary i2c listener, fixed loop
    Rearranged a couple of functions from the serial input function to be
    back in the loop where they belong. Added a rudimentary i2c listener
    that should allow for parameter updates, but will only reply with "OK"
    for now
    Progress on:
    - https://github.com/pyr0ball/pyr0piezo/issues/2
    - https://github.com/pyr0ball/pyr0piezo/issues/22
    [Pyr0_Piezo_Sensor_v2.x.x.ino]
2019-03-16 fixed syntax preventing compilation
    [Pyr0_Piezo_Sensor_v2.x.x.ino]
2019-03-18 Added wiring diagrams, fixed docs
    - Added wiring diagram for RAMPS
    - Added wiring diagram for Creality OEM Board
    - Changed Marlin firmware config to use Active Low logic
    Progress on https://github.com/pyr0ball/pyr0piezo/issues/14
2019-03-18 Added wiring diagram for DuetWifi
    Also fixed transparency on other wiring diagrams
    progress on https://github.com/pyr0ball/pyr0piezo/issues/14
2019-03-18 Added hookup guides for common MKS boards
    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
2019-03-23 sync all boards for Rev.2.0.1 before gerberization
    - added test pads for debugging amp circuit
    [Pyr0-Piezo-FFC-Creality-X-Board.2.0.1.brd, Pyr0-Piezo-FFC-Creality-X-Board.2.0.1.sch, Pyr0-Piezo-Standalone_2.0.1.brd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]
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2019-03-27 Renamed X-car breakout for direct feed.
    incoming design for bowden style extruders
    [Pyr0-Piezo-FFC-Direct-Creality-X-Board.2.0.0.brd, Pyr0-Piezo-FFC-Direct-Creality-X-Board.2.0.0.sch, Pyr0-Piezo-FFC-Direct-Creality-X-Board.2.0.1.brd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]
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2019-04-12 Updated eagle files for 1.0.2 for Eagle 9.0.2
    [Pyr0-Piezo-Standalone1.0.2.brd, Pyr0-Piezo-Standalone1.0.2.sch]
2019-04-12 Adjusted capacitor placement for easier soldering
    Also optimized traces and ground plane
    [Pyr0-Piezo-Standalone_2.0.1.brd]
2019-04-22 fixed unary operators for adjustment logic
    - Switched unary operators to correct syntax (+= vs =+) Should fix oscillation noted in https://github.com/pyr0ball/pyr0piezo/issues/24
    - Added software hysteresis to the adjustment function. Referenced in https://github.com/pyr0ball/pyr0piezo/issues/24
    - Fixed notes to show the correct gain factors
    [Pyr0_Piezo_Sensor_v2.x.x.ino]
2019-04-22 migrated floats to #define values
    for more efficient compilation, switched float values set in initial config to definitions that are immediately computed into integers, which cut down on flash usage. also removed non-working debug float outputs for VCompRef and vAdjRead as stated in https://github.com/pyr0ball/pyr0piezo/issues/20
    [Pyr0_Piezo_Sensor_v2.x.x.ino]
2019-04-22 Converting to defines and else ifs
    Defines save flash and progmem and elseifs increase execution speed on code repeated on every loop.
    Side note, something funky happened with the spacing. Fixed it, but it's slightly different than what it was before.
    [Pyr0_Piezo_Sensor_v2.x.x.ino]
2019-04-22 Fixing debug vars in case they ever want to be used again
    Integer result needs to be cast to a float to obtain a float result from division.
    [Pyr0_Piezo_Sensor_v2.x.x.ino]
2019-04-22 Fixes for oscillating PWM output
    - Added hysteresis input for UART/I2C
    - Fixed example to show correct command (VADJ vs VADJH)
    - added TRG_DUR to the interrupt function
    - Migrated math for 8-10bit ADC to a different function
    - Organized/added debug serial output
    - fixed line begin whitespace
    [Pyr0_Piezo_Sensor_v2.x.x.ino]
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2019-04-22 Set I2C input to be toggled by def
    -Synced Comp/Vref til #24 is fixed
    [Pyr0_Piezo_Sensor_v2.x.x.ino]
2019-06-11 for v2.x this fixes https://github.com/pyr0ball/pyr0piezo/issues/28
    [Pyr0_Piezo_Sensor_v2.x.x.ino]
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2019-06-11 fixed names for new files
    [Pyr0_Piezo_Sensor_v2.x.x.ino]
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2019-06-26 fixed some ordering causing definition issues
    - started on https://github.com/pyr0ball/pyr0piezo/issues/30
    [Pyr0_Piezo_Sensor_v2.x.x.ino]
2019-06-27 Fixed "Flappy DAC" bug in rev.2.x.x firmware
    - Fixed https://github.com/pyr0ball/pyr0piezo/issues/26
    - Changed adjustment logic to be calculated based on Vcc rather than ADC reference, which was causing issues in the mathematical functions, resulting in negative number outputs
    - Migrated to internal vRef, fixed https://github.com/pyr0ball/pyr0piezo/issues/23
    - Eliminated floats, fixing https://github.com/pyr0ball/pyr0piezo/issues/31
    - This required addition of long, however
    - Fixed https://github.com/pyr0ball/pyr0piezo/issues/20
    [Pyr0_Piezo_Sensor_v2.x.x.ino, pP_function.h, pP_pins.h]
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2019-07-06 Created variable for voltmeter constant, fixed whitespace a bit
    [Pyr0_Piezo_Sensor_v2.x.x.ino, pP_function.h]
2019-07-06 Complete overhaul of i2c code, created library structure
    - Progress on https://github.com/pyr0ball/pyr0piezo/issues/30
    - ToDo: Create master library for easy integration with other firmwares
    [pP_i2c.cpp]
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2019-07-06 Added i2c input handler for long variable
    - Progress on https://github.com/pyr0ball/pyr0piezo/issues/22
    [pP_i2c.cpp]
2019-07-19 Changed compiler behavior for i2c. I2C library is still broken
    - Firmware does still compile correctly when I2C is disabled
    [pP_i2c.cpp]
2019-07-25 Migrated from single 60pin FFC to combined 15+40p
    - 60pin cables are nearly impossible to source in longer sizes
    - both 15p-1mm and 40p-0.5mm are readily available as one is used for
    Raspberry Pi cameras, and the other is used for eDP and LVDS
    - This method also allows for more ground return paths and better
    voltage distribution
    [Pyr0-Piezo_Direct-Extruder-FFC-Breakout_2.1.1.brd, Pyr0-Piezo_Direct-Extruder-FFC-Breakout_2.1.1.sch]
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2019-07-25 Moved to dual FFC cable (15p-1MM + 40p-0.5mm)
    [Pyr0-Piezo_Direct_Extruder_Board2.1.1.brd, Pyr0-Piezo_Direct_Extruder_Board2.1.1.sch]
2019-07-25 Added issue template for requesting a new mount
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2019-08-15 fixed some file encoding issues
    [Pyr0-Piezo-Standalone_2.0.2.brd, Pyr0-Piezo-Standalone_2.0.2.sch, Pyr0-Piezo-Standalone_2.1.1.brd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]
2019-08-29 commented out main loop trigger reset #bugfix
    After switching to the new scheduler, the main loop was resetting the
    trigger too quickly. Migrating reset to the pulse trigger function
    instead
    [Pyr0_Piezo_Sensor_v2.x.x.ino]
2019-08-29 fixed definition parameter for I2C config #bugfix
    [pP_config.h]
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2019-08-29 Slight adjustment to wire routing for better spacing #bugfix
    [Pyr0-Piezo-Standalone_2.1.1.brd]
2019-08-29 fixed footprint for RGB LED (default polarity was backwards) #bugfix
    [Pyr0-Piezo-Standalone_2.1.1.brd]
2019-08-30 fixed incorrect resistor values on FFC Direct vreg #bugfix
    [Pyr0-Piezo_Direct-Extruder-FFC-Breakout_2.0.1.brd, Pyr0-Piezo_Direct-Extruder-FFC-Breakout_2.0.1.sch, Pyr0-Piezo_Direct-Extruder-FFC-Breakout_2.1.1.brd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]
2019-08-30 fixed 0606 rgb led footprint #bugfix
    [Pyr0-Piezo-Standalone_2.1.1.sch]
2019-08-30 new version EasyPiezi-v2.1.2 - adds extra test points #featureadd
    [Pyr0-Piezo-Standalone_2.1.2.brd, Pyr0-Piezo-Standalone_2.1.2.sch]
2019-09-25 synced nomenclature for vfollower variables #bugfix
    [Pyr0_Piezo_Sensor_v2.x.x.ino, pP_function.h, pP_i2c.cpp]
2019-09-25 more syntax fixes (from merge) #changelog
    [pP_function.h]
2019-09-26 fixed syntax error in includes section
    [Pyr0_Piezo_Sensor_V2.x.x.cpp]
2019-09-29 Reverted voltmeter code #bugfix
    [Pyr0_Piezo_Sensor_V2.x.x.cpp, pP_function.h]
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2019-09-30 Fixed serial command for voltmeter constant, added EEPROM support for it #bugfix
    [pP_config.h]
2019-10-02 Added new test points to programmer jig #featureadd
    [Pyr0-Piezo-Standalone_2.1.2.brd, Pyr0-Piezo-Standalone_2.1.2.sch, Pyr0-Piezo_AVR_Board_Programmer_2.1.2.brd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]
2019-10-05 analogWrite is replaced with native phase correct PWM, 4kHz 10-bit on comparator and 16kHz 8-bit on voltage follower #changelog
    [Pyr0_Piezo_Sensor_V2.x.x.cpp, pP_function.h]
2019-10-09 Complete overhaul of FFC board for v2.1.2 #bugfix
    [Pyr0-Piezo_AVR_Board_Programmer_2.0.1.brd, Pyr0-Piezo_AVR_Board_Programmer_2.1.2.sch, Pyr0-Piezo_Direct-Extruder-FFC-Breakout_2.1.1.brd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]
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2019-10-10 added documentation category to docs script #docs
    also fixed a couple of minor text errors
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2019-10-11 Added silkscreen of board revision for EzPz #featureadd
    - fixes https://github.com/pyr0ball/pyr0piezo/issues/39
    [Pyr0-Piezo-Standalone1.0.1.brd, Pyr0-Piezo-Standalone1.0.1.sch, Pyr0-Piezo-Standalone1.0.2.brd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]
2019-10-12 Added beginning of doc explaining circuit settings #docs
    - begin work on https://github.com/pyr0ball/pyr0piezo/issues/45
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2019-10-16 Created DIY standalone board for use with external MCU #featureadd
    - Starts work on https://github.com/pyr0ball/pyr0piezo/issues/46
    [Pyr0-Piezo-v2-DIY-Standalone-Board_v1.0.0.brd, Pyr0-Piezo-v2-DIY-Standalone-Board_v1.0.0.sch]
2019-10-16 fixed polarity for trigger LED on DIY board #bugfix
    [Pyr0-Piezo-v2-DIY-Standalone-Board_v1.0.0.brd, Pyr0-Piezo-v2-DIY-Standalone-Board_v1.0.0.sch]
2019-10-24 renamed Eagle Files to reflect product name #docs
    [EasyPiezi1.0.1.brd, EasyPiezi1.0.1.sch, EasyPiezi1.0.2.brd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]
2019-10-24 Added page for PT100 RTD sensor #docs
    - Starts work on https://github.com/pyr0ball/pyr0piezo/issues/44
2019-10-25 new major version for addressing #48 #featureadd
    - Swapped PZ1 input header from 2pin to 3pin
    - Attached PZ_DET to PC2/PCINT10
    [EasyPiezi_2.2.0.brd, EasyPiezi_2.2.0.sch]
2019-10-27 fixed definition preventing serial response in #49 #bugfix
    [Pyr0_Piezo_Sensor_V2.x.x.cpp]
2019-10-28 Fix clearing stored config on restore
    [pP_function.h]
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2019-10-29 Fixed config reset #54 #bugfix
    [pP_config.h]
2019-10-30 Fix EEPROM saving issue when issuing a RESET command via a serial terminal.
    [pP_config.h]
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2019-10-31 These code changes are for resetting the config values to the default values by issuing the ERASE word via a serial terminal.
    This change was made for clarity sake, as ERASE stands out more than the previous RESET word, which could be mistaken for just rebooting the board.
    [Pyr0_Piezo_Sensor_V2.x.x.cpp, pP_config.h]
2019-11-05 Fixed width of thermals on singledisk adapter #bugfix
    [Pyr0-Piezo_SingleDisk_Adapter.brd]
2019-11-06 Fixed pad thermals, added url, fixed logo #bugfix
    [EasyPiezi_2.2.0.brd, EasyPiezi_2.2.0.sch]
2019-11-13 Adds support for inverting trigger logic. #featureadd
    - Addresses #61
    [pP_config.h, pP_function.h]
2019-11-26 Fix for gain adjustment #bugfix
    [pP_function.h]
2019-12-19 fixing serial input not taking effect immediately #bugfix
    Not a complete fix, still needs work
    [pP_function.h]
2019-12-19 fixed accidental reversal of gain adjust #oops
    [pP_function.h]
2019-12-19 Revert "fixed accidental reversal of gain adjust #oops"
    This reverts commit 3dcadb5e4ee9449eafdcd9f9861ba8b142373eb1.
    [pP_function.h]
2019-12-31 fixed platformio.ini to allow build and upload directly #bugfix
    [pP_function.h]
2019-12-31 fixed logic and pzdet inputs #bugfix
    [Pyr0_Piezo_Sensor_V2.x.x.cpp, pP_function.h]
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2020-01-11 fixed typo in link to uart pdf #docs
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2020-01-16 changed error LED behavor to instead indicate a trigger event #featureadd
    [Pyr0_Piezo_Sensor_V2.x.x.cpp, pP_function.h]
2020-01-17 fixed syntax issue with version variable #bugfix
    [Pyr0_Piezo_Sensor_V2.x.x.cpp]
2020-01-17 fixed new led behavior, was toggling instead of blipping #bugfix
    [Pyr0_Piezo_Sensor_V2.x.x.cpp, pP_function.h]
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2020-01-21 updated v2.2.0 eagle files with latest library parts #bugfix
    [EasyPiezi_2.2.0.brd, EasyPiezi_2.2.0.sch]
2020-01-21 gave singledisk pcb a bit more flex for better sensitivity #bugfix
    [Pyr0-Piezo_SingleDisk_Adapter_3pin.brd, Pyr0-Piezo_SingleDisk_Adapter_3pin.sch]
2020-01-23 updated piezoPCB singledisk for better actuation #bugfix
    [Pyr0-Piezo_SingleDisk_Adapter_3pin.brd, Pyr0-Piezo_SingleDisk_Adapter_3pin.sch]
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2020-02-06 Attempt at fixing compile error
    [pP_config.h, pP_function.h]
2020-02-26 Added support for either 5v or 3.3v operation #featureadd
    - Addresses #67
    - Uses one additional pin + 3 additional resistors + LM317L
    [EasyPiezi_2.3.0.brd, EasyPiezi_2.3.0.sch]
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2020-02-27 Added code for switching between 3.3v and 5v signal output #featureadd
    - Fixes #67
    [Pyr0_Piezo_Sensor_V2.x.x.cpp, pP_config.h, pP_function.cpp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]
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2020-04-14 Correct I2C port now used, fixed config and state reply
    [pP_config.h, pP_i2c.cpp]
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2020-04-27 Fixed links to images in a couple of pages #docs
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2020-05-07 Added user-friendty VCC readings adjustment #featureadd Minor fixes to i2c #bugfix
    [i2c.cpp, pP_i2c.cpp]
2020-05-09 fixed incorrect annotation on one config #docs
    [pP_config.h]
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2020-05-13 fixed i2c docs links #docs
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2020-05-13 fixed i2c byteslength for some inputs #docs
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2020-05-21 fixed schematic headers for kitspace
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2020-06-14 Changed logic default to low instead of high #bugfix
    [pP_config.h]
2020-06-15 added fallback version parameter. Fixes #73 #bugfix
    [pP_config.h]
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2020-06-23 fixed missing precompiler flag in i2c for 328p variants #bugfix
    [pP_i2c.cpp]
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2020-07-24 fixed component values and names for v2.3.0 #bugfix
    [EasyPiezi_2.3.0.brd, EasyPiezi_2.3.0.sch]
2020-07-24 new board v2.3.1 - Moves larger components to top of board #bugfix
    - also optimizes several silkscreens and trace routes
    [EasyPiezi_2.3.1.brd, EasyPiezi_2.3.1.sch]
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2020-07-30 #bugfix Fixed problem with config resetting on every boot, minor fix to i2c communication
    [pP_config.h, pP_i2c.cpp]
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2020-07-30 fixed links on menu and images for wiring harness #docs
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2020-08-20 Increased size of bypass jumper on EasyPiezi for easier soldering #bugfix
    [EasyPiezi_2.3.1.brd, EasyPiezi_2.3.1.sch]
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2020-09-14 Fixed Heater trace to ground on EzPzEffector #bugfix
    [EzPz-Effector_v2.3.1.brd, EzPz-Effector_v2.3.1.sch]
2020-09-15 Added bypass jumper to allow powering EzPz direct from heater VCC #featureadd
    [EzPz-Effector_v2.3.1.brd, EzPz-Effector_v2.3.1.sch]
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2020-09-15 set default vccsw state to 5v instead of 3.3v #bugfix
    default parameters do not work on 3.3v
    [pP_config.h]
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2020-09-29 New HW rev v2.3.2 - changes method for adjusting output voltage level #bugfix #featureadd
    - Switches back to L78## fixed voltage regulators as they perform much better at 24v
    - Changes the resistor array previously used by LM317 to adjust VCC to
    now adjust output signal voltage only
    - Added better thermals for VReg
    - Optimized several groundplanes and polys
    [EasyPiezi_2.3.2.brd, EasyPiezi_2.3.2.sch]
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2020-10-08 fixed readme contribution section with current workflows #docs
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2021-08-26 Added compiled binary for v2.3.2, edited serial to reduce memory use #bugfix
    [pP_config.h]
2022-09-17 Fixed trigger duration, fixed blinking
    [Pyr0_Piezo_Sensor_V2.x.x.cpp, pP_config.h, pP_function.cpp]

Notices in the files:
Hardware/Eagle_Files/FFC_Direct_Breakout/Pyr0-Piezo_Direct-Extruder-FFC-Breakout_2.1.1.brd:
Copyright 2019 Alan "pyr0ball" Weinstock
